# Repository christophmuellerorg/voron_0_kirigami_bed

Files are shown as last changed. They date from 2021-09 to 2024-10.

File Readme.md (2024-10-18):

# What is this?

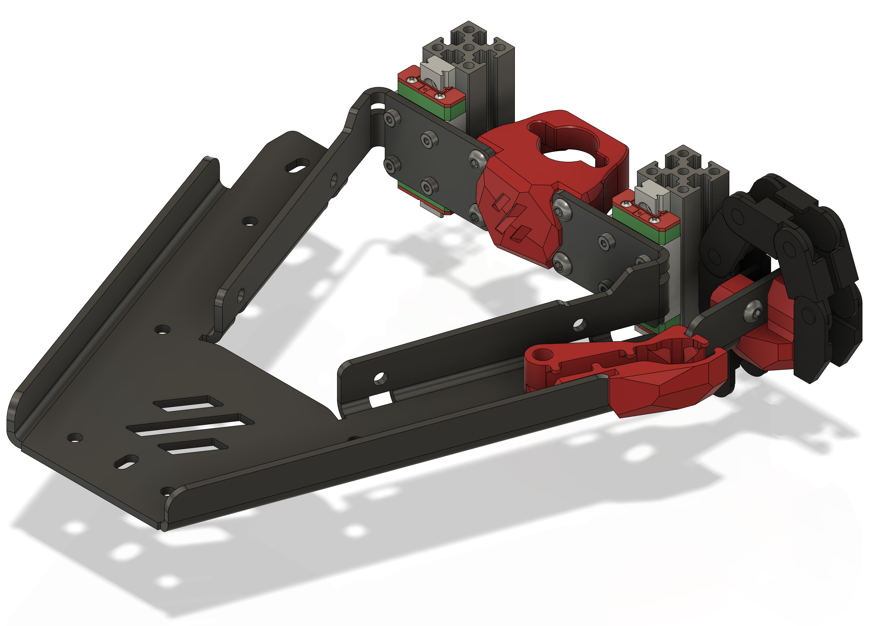
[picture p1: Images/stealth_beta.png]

A laser cut and bent single piece bed concept, trying to implement a lightweight and stiff bed with full access to the mounting screws.

# Where can I get it? 

I only did a small prototype run and will not be able to sell it myself, however there are a few Voron related shops that started stocking it:

- [Deepfriedhero](https://dfh.fm/products/kirigami-beds?variant=43382871556318) (US) 
- [Fabreeko](https://www.fabreeko.com/products/voron-v0-1-kirigami-bed-kit-by-ldo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) (US)
- [3dmakerparts](https://3dmakerparts.com/products/voron-0-1-kirigami-bed) (US)
- [Printyplease](https://www.printyplease.uk/LDOKiri) (UK)
- [Lecktor](https://lecktor.com/en/v0-buildplate/905-kirigami-bed.html) (EU)
- [Unique Prints](https://uniqueprints.shop/shop/buildplate/kirigami-bed-upgrade-for-voron-v0-1/) (AU)
- [Zen3D](https://shop.zen3d.eu/ldo-kirigami-bed-mount-kit) (EU)

I will add additional suppliers _with a vendor role on the Voron discord_ - please contact me on discord or create a pull request with your discord ID.

# Which plastic parts do I need to print?
 
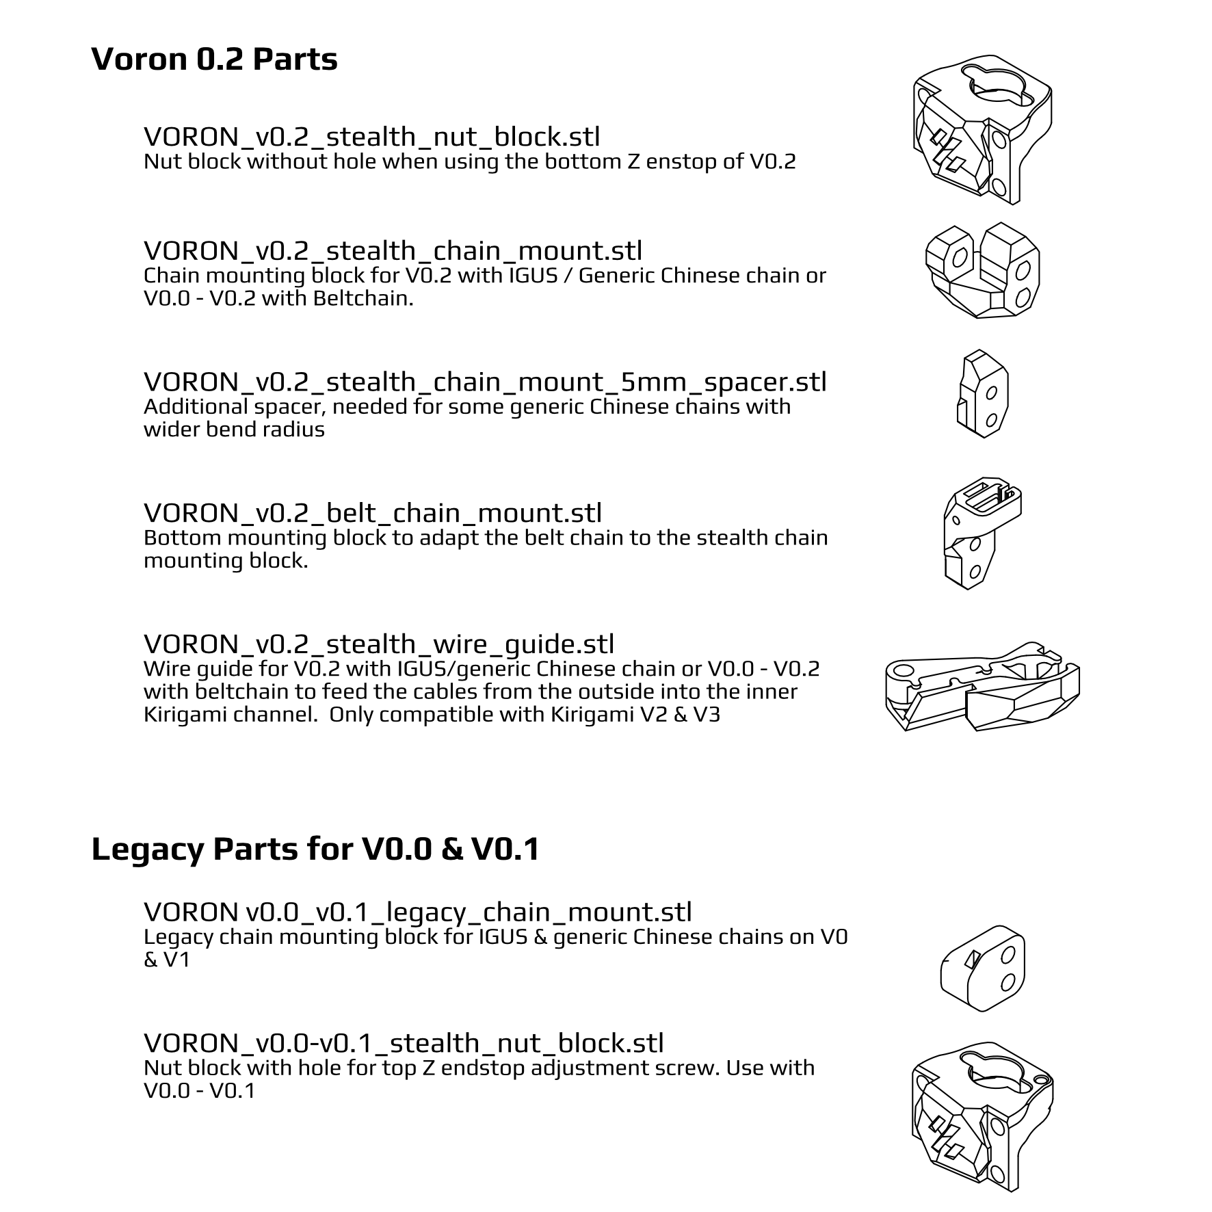
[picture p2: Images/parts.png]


# License

The sheet metal part is available under [CC-BY-SA 4.0](https://creativecommons.org/licenses/by-sa/4.0/) AND [GPL V3.0](https://www.gnu.org/licenses/gpl-3.0.de.html). The plastic parts are partially derived from the existing Voron parts and hence follow the same License, [GPL V3.0](https://www.gnu.org/licenses/gpl-3.0.de.html). 

This means you are allowed to modify and share the sheet metal part under either license, as long as you credit me with a link to this Github repository. You are allowed to produce and sell the part without royalties, a donation on [vorondesign.com](https://vorondesign.com) to fund future development of the Voron project is however appreciated.

# Kiriwhat?

<https://en.wikipedia.org/wiki/Kirigami>

# BOM
- 1x Kirigami Bed
- 8x M2x4 to mount the bed to the carriages
- 4x M3 Heatsets + 4x M3x6 screws for the leadscrew mount
- 4x M3 Heatsets + 2 M3x6 screws for the chain mount
- 1x M3 Heatset + 1 M3x6 screw for the wire guide

# Versions
- V2: added a cutout for the thermal fuse
- V3: slots instead of holes for the bed springs, allowing to adjust the Y offset over a 3mm range to support V0.0 as well as the sherpa mini mod. 

# Installation
The guys from Maple Leaf Makers made a nice tutorial on how to convert the stock bed to Kirigami.

Video tutorial to convert the stock bed to Kirigami (https://www.youtube.com/watch?v=eOnNvhircn8)

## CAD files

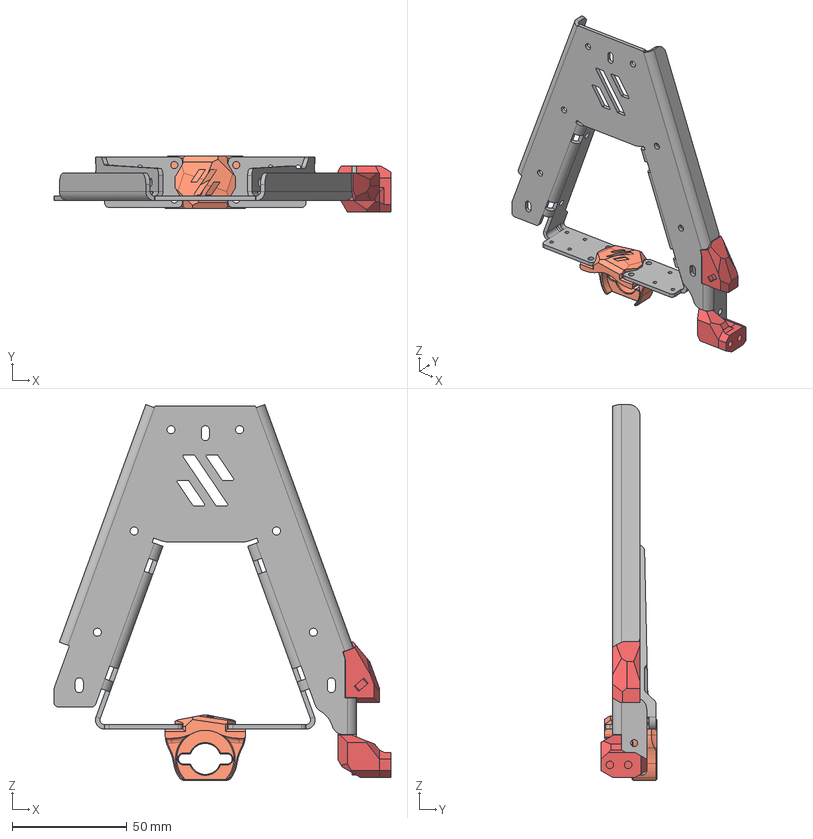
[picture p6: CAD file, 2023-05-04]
CAD/Kirigami_V0.2_stealth_chain_release.step
147.0 x 24.5 x 164.1 mm
VORON_v0.2_stealth_nut_block v3
VORON_v0.2_stealth_chain_mount v2
V0_sheet_metal_bed_v2 v66
VORON_v0.2_stealth_wire_guide.stl v2
VORON_v0.2_stealth_chain_mount_5mm_spacer v2

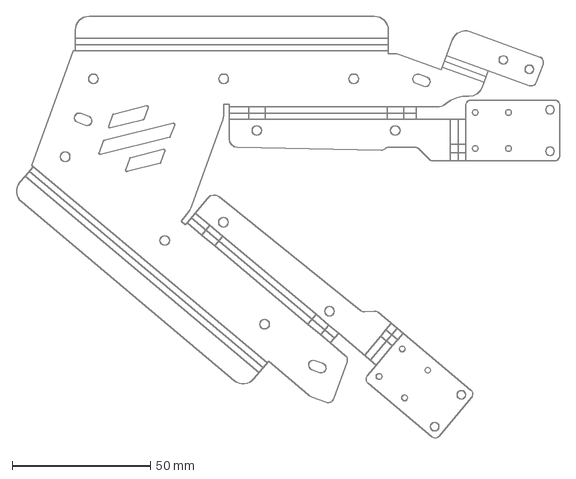
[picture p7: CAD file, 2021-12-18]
CAD/V0_sheet_metal_bed_v3.dxf
196.2 x 152.6 mm

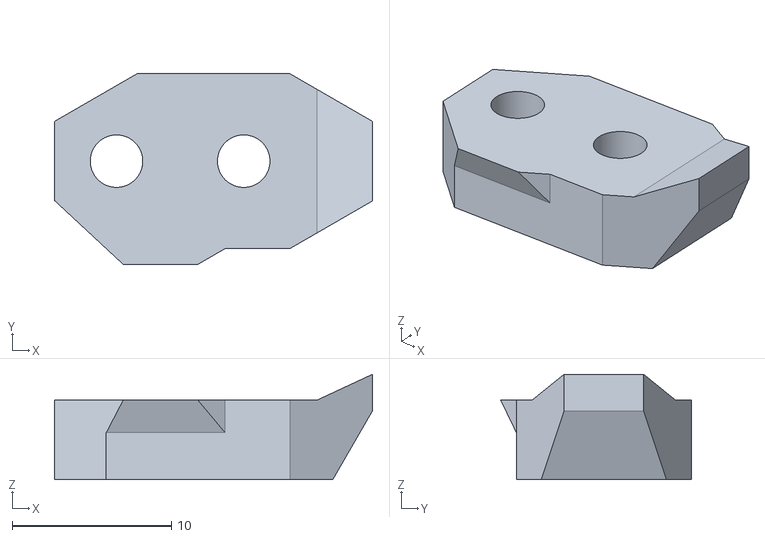
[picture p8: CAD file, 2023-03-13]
STL/VORON_v0.2_stealth_chain_mount_5mm_spacer.stl
20.0 x 12.0 x 6.63

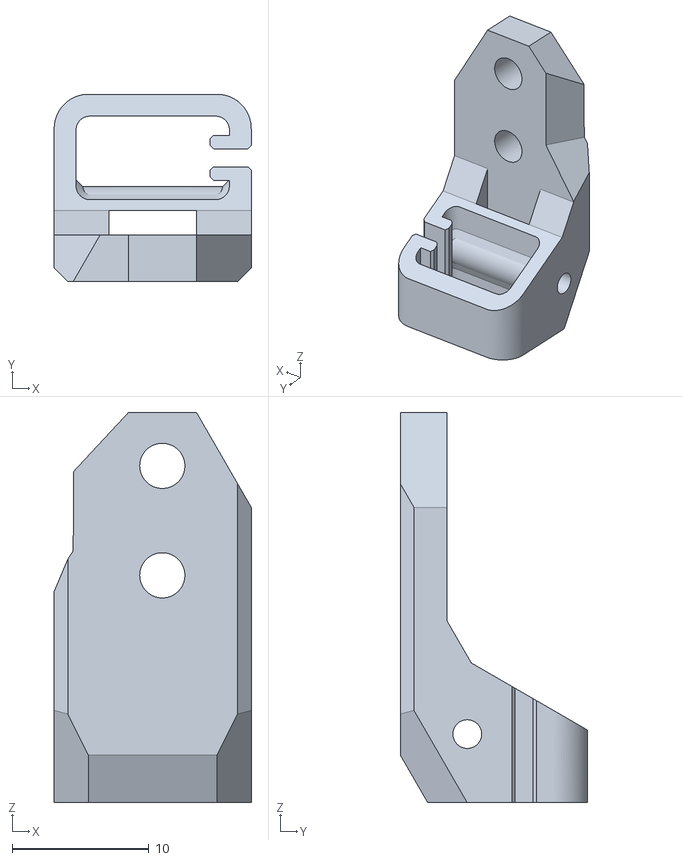
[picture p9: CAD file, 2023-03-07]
STL/VORON_v0.2_belt_chain_mount.stl
14.4 x 13.7 x 28.5

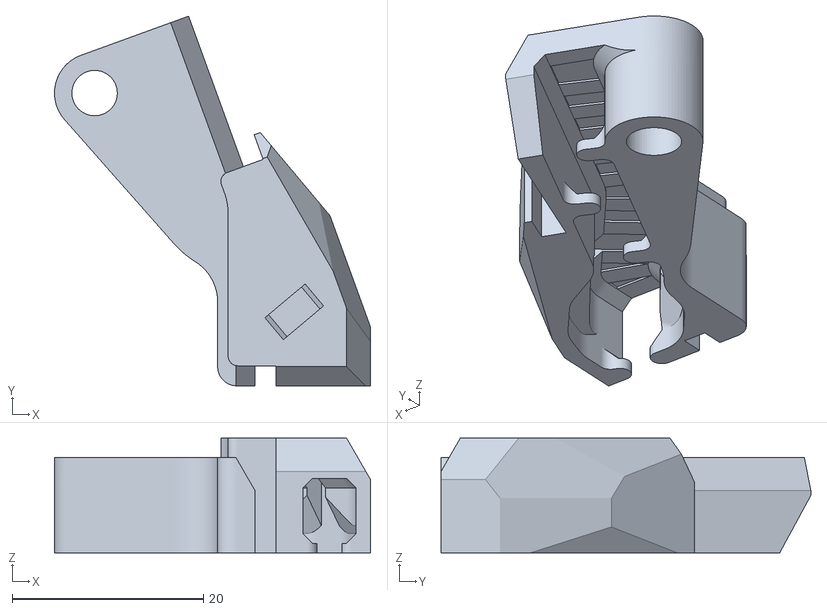
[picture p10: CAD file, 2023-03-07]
STL/VORON_v0.2_stealth_wire_guide.stl
33.1 x 38.7 x 12.0

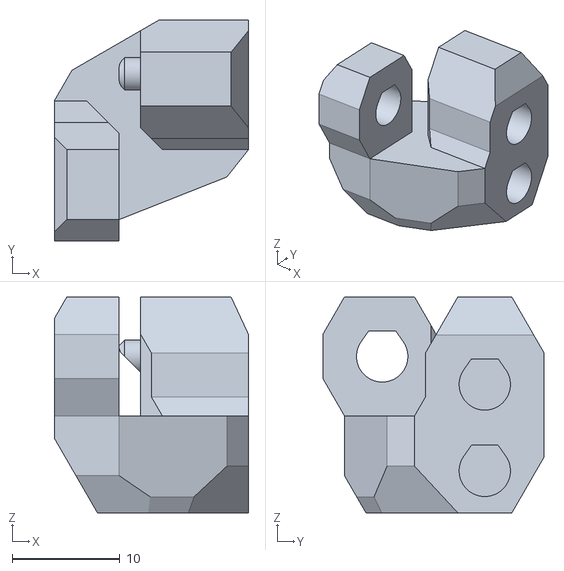
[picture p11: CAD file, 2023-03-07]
STL/VORON_v0.2_stealth_chain_mount.stl
18.0 x 20.5 x 20.0

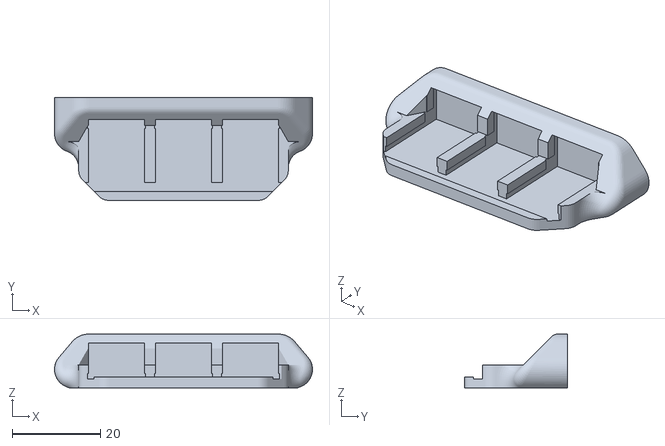
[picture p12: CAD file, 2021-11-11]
STL/kirigami_wago_mount.stl
58.4 x 23.2 x 12.2

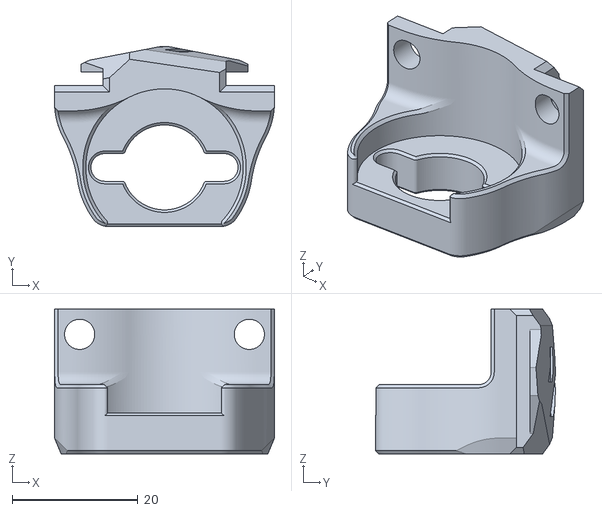
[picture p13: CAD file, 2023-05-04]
STL/VORON_v0.2_stealth_nut_block.stl
35.0 x 28.6 x 23.0

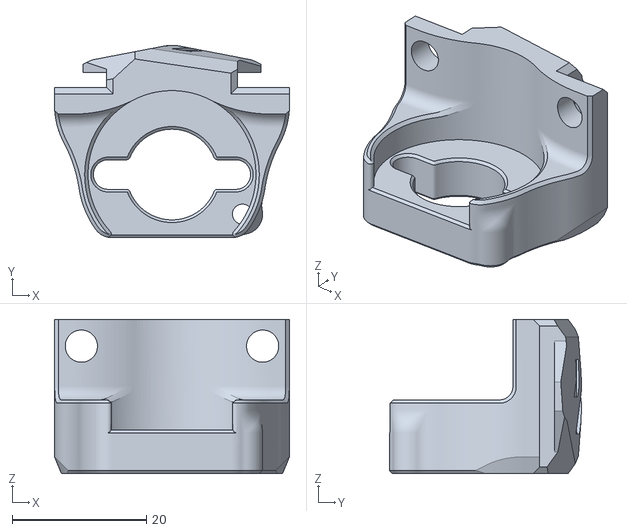
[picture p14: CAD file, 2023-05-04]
STL/VORON_v0.0-v0.1_stealth_nut_block.stl
35.0 x 28.6 x 23.0

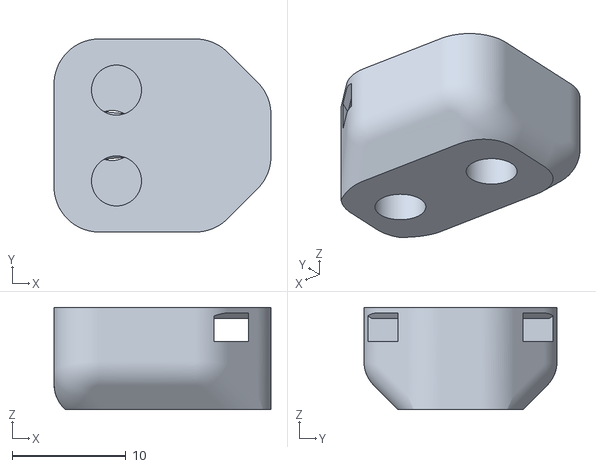
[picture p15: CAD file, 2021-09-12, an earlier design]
STL/VORON v0.0_v0.1_legacy_chain_mount.stl
19.1 x 17.0 x 9.00

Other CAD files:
CAD/Kirigami_V0.2_stealth_chain_release.f3d
CAD/V0_sheet_metal_bed_v3.f3d
CAD/kirigami_wago_mount.f3d

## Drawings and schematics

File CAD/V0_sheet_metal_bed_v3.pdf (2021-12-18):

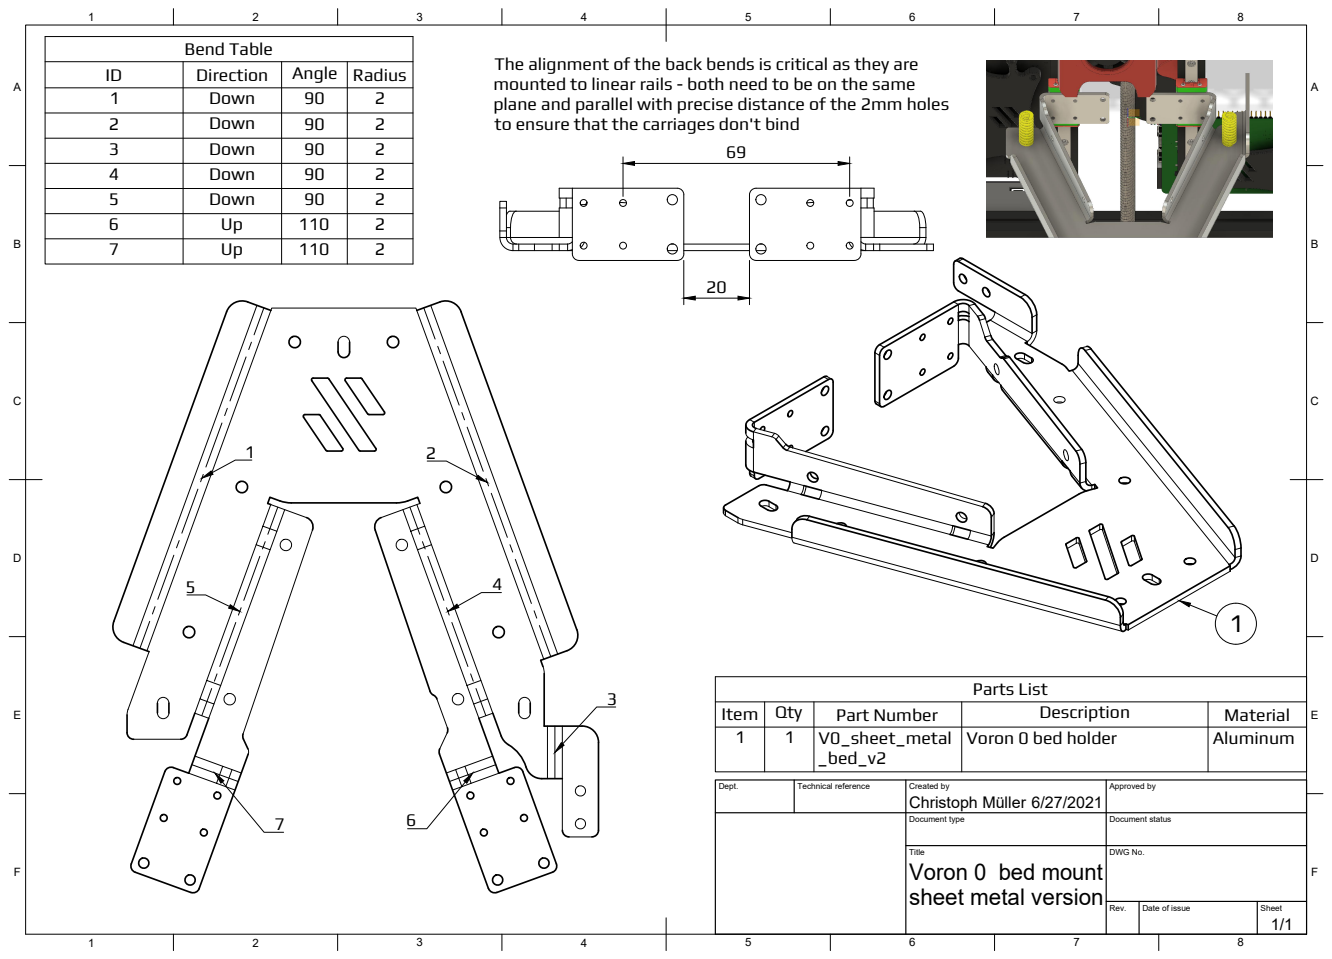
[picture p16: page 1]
Title; DWG No.; Rev.; Date of issue; Sheet; Bend Table; Parts List

The alignment of the back bends is critical as they are
mounted to linear rails - both need to be on the same
plane and parallel with precise distance of the 2mm holes
to ensure that the carriages don't bind

ID | Direction | Angle | Radius
1 | Down | 90 | 2
2 | Down | 90 | 2
3 | Down | 90 | 2
4 | Down | 90 | 2
5 | Down | 90 | 2
6 | Up | 110 | 2
7 | Up | 110 | 2

Item | Qty | Part Number | Description | Material
1 | 1 | V0_sheet_metal _bed_v2 | Voron 0 bed holder | Aluminum

Dept. | Technical reference | Created by Christoph Müller 6/27/2021 | Approved by

Document type | Document status

Voron 0 bed mount
sheet metal version

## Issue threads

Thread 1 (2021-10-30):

the belt z axis mod

dukeGreen, 2021-10-30:
Do you play to support the belt z axis mod?

christophmuellerorg, 2021-11-15:
I won't support it myself, but there is one available here: https://github.com/VoronDesign/VoronUsers/tree/master/printer_mods/MathematicalPotato/v0.1_belted_z_drive/STL/Kirigami_Bed_Mount

Obviously I have not tested it.

Closed 2021-11-20.

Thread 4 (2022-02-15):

Incorrectly sized heat set insert holes on igus_chain_mount.stl

austinvojta, 2022-02-15:
Chain mount piece has 4.4mm diameter holes for heat set inserts. Voron standard for the BOM inserts is 4.7mm (regardless of orientation).

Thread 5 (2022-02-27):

Rail Mounting Screw Spacer

marc-gist, 2022-02-27:
Not an issue, love the mod! Thank you!
That said.  I did print a ~2mm spacer so that I could use the M2x6 screws I already had from the kit for mounting rails.
I think making something like this part of your repository can help those who don't know how to use Fusion to quickly make something like I did from the v0 CAD.

Again, thank you!

Closed 2023-01-04.

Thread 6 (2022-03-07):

stability issues (mounting problem, material?)

dmnkhhn, 2022-03-07:
Hello there,

it's maybe not a general issue but I have stability issues with my Kirigami bed made from 2mm AW5754 (aluminum).

When mounted I can easily push down the front of the bed just by applying little force on the front edge.
This also happens when I adjust the front screw making first layer a hit and miss.

Based on your experience, what might cause this?
Incorrect mounting (screws too loose), incorrect material, rails too sloppy?

I had to use some rather cheapish M2x4mm screws with tiny heads and I have ordered some better ones now. Still I would like to rule out other possibilities.

Any help is appreciated :-)

dmnkhhn, 2022-03-17:
This is still an issue after changing to new rails with a higher preload and new screws that are fully tightened now. I can see it moving when I touch it slightly with one finger. Might be a material issue?

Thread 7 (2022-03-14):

Issues with bed installation

ModMike, 2022-03-14:
Before I describe my issue, let me state, for the record, that I understand this issue has NOTHING to do with you, I am just looking for advice on how to install the bed properly.

I am having a serious issue with binding. Once the bed is tightened the rails rails bind because they are forced out of plane by the bed mounts. I tried tweaking the mounting ears to be in plane, then I designed and printed a part to clamp and the ears, but it only helped a little. Even you tubers such as Vecto 3D had the same issue during his stream, you can see it in his [video](https://www.youtube.com/watch?v=X-Wu85DuZxQ&t=9142s) at the 30 minute mark. He ended up using some TPU spacers but still had binding.

The problem is that factory tolerances and material flexibility make it so that mounting ears are out of plane. The first one I got was beyond tweaking. The replacement I received was better but still binds.

How do you recommend I fix this issue? For now, I ordered 2mm O-Rings to  put between the bed and the rails. I am hoping I can I can toque the screws in different amounts to align the carriers their rails. I just hope to be able to tighten them enough to remove any movement caused by flex between the two.

Let me know your thoughts, my V0.1 has been sitting around for 3 months.

Thanks!

christophmuellerorg, 2023-01-04:
This is not typical, but I have seen some really bad tolerances on steel beds on Aliexpress (looking at you, Funssor...) which would easily cause serious issues due to the bends being out of spec. Check whether the flaps are in one plane and parallel to each other and verify whether the distance between both ends is 20mm - if not contact your vendor, it's a quality control issue on their side.

Closed 2023-01-04.

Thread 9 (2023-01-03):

JST connectors missing from the BOM

KreativeLabs, 2023-01-03:
I purchased this kit but 2pcs JST connectors are missing feom the list to be able to split the thermistor wires. I didn’t have those at hand so I have to pause the conversion. Do I misunderstand something about the build?

christophmuellerorg, 2023-01-04:
The PCB is not part of the Kirigami bed project but an addition by LDO I have no control over.

KreativeLabs, 2023-01-04:
Oh I see :)

Closed 2023-01-04.

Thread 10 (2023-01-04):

STL' corrupted?

bsjoelund, 2023-01-04:
Downloaded the stl's and no file can be opened in any slicer.

christophmuellerorg, 2023-01-04:
Nothing has changed and the files are fine, just tried - likely user error, try the download zip option of the "code" button on the repository main page.

Closed 2023-01-04.

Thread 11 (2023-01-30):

Material type not mentioned in README

west1012, 2023-01-30:
Hi.  Would it be possible to get the material type chosen (I am guessing 5052 aluminum) in the README.md for the project?  I see in the PDF file in the CAD file the part is to be made out of "aluminum", but it took me a while to see it there.  I'm guessing I'm not the only one who hasn't been able to find it before.

Thanks!

VersedHG, 2023-05-29:
LDO use 6061 alu.

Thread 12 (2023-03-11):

Chain mount problem - chain radius too small

hmouridsen, 2023-03-11:
Hi

I think the [VORON_v0.2_stealth_chain_mount.stl] should be a little bigger. I don't know if chains are different, but I've bought the one listed in the 0.2 bom. I feel the bending radius is too small for the chain, witch means my printer struggles with the z-axis due to chain resistance
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

christophmuellerorg, 2023-03-11:
Hi, can you measure the distance between the profile and the inside of your chain for the worst possible configuration, i.e. the top chain segment being parallel to the ground?

Technically this mount is already widened relative to the original design and based on the chains I have here it should just fit. I might add a dragchain spacer to add a few additional mm if required.

Best,
Christoph

hmouridsen, 2023-03-12:
Hi Christoph

First of all thanks for sharing your work.

I'm not sure if I understand you clearly, but I for my chain to move freely, without resistance, I need 2mm more. Witch means the chain mount should be 12mm instead of 10mm. A spacer could be an easy solution as well.

My chain starts to move freely at 27mm bend radius (with the top link parallel to the ground), and at the moment I measure about 24mm

At first I mounted the 0.1 chain mount witch is 9mm wide, and it made my z motor buzz.

hmouridsen, 2023-03-12:
Hi

I did some spacer testing, and 15mm seems to be the correct size for my chain, but I guess it can vary a lot from chain to chain

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

christophmuellerorg, 2023-03-13:
I just added a 5mm spacer, please give it a try and let me know whether it works.

hmouridsen, 2023-03-15:
> I just added a 5mm spacer, please give it a try and let me know whether it works.

Thanks a million - it's perfect - chain is absolutely moving freely now

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

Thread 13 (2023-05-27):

v0.2 belt chain mount question

chrisheninger, 2023-05-27:
Hi Christoph (or anyone reading these issues that might know the answer!)–

I'm building a v0.2 kit from Formbot3d.

It came with a kirigami bed– and I'm trying to figure out where the `VORON_v0.2_belt_chain_mount` belongs. I've noticed a lot of the pictures/diagrams in the repo show different variations/versions and I haven't seemed to be able to find anything online showing different angles of the v0.2.

Here's a photo:

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

Thank you!

Edit: After thinking about it a little longer... I'm realizing that I don't need the "belt chain mount" because I'm using the "stealth chain mount" and spacer?

YungChin95, 2023-05-29:
Yes, the belt chain mount is if you're using the Belt Chain usermod. So it's not needed for you

Closed 2023-05-29.

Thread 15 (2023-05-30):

Tools stl directory

ningpj, 2023-05-30:
Your earlier release included a tools subdir with k-bed bender and dual rail alignment jig.
Did you mean to drop it when you published the updated version? No problem if you did, just checking.

Closed 2024-11-06.

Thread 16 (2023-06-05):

Formbot bed is too thick for the Stealth Nut Block

Janus303, 2023-06-05:
We are building the V0.2 kit from FormBot, which comes with a kirigami bed. The Stealth Nut Block part will not fit, even before installing heat set inserts. It may be due to the thickness of the powder coat. I would like to edit that part to make it a little roomier, but I am not seeing the CAD file.

Kagee, 2023-06-05:
The nut block is part of [Kirigami_V0.2_stealth_chain_release.f3d](https://github.com/christophmuellerorg/voron_0_kirigami_bed/blob/master/CAD/Kirigami_V0.2_stealth_chain_release.f3d).

The CAD calls for 2.0 mm and a 20 mm gap. What are the measurements on the FormBot kit? LDO kit is a hair's breath *below* spec.

Janus303, 2023-06-06:
The thickness when measured from top to bottom is 2.5mm. The thickness when measured in the middle is 2.3mm. So there is a bit of a bow, but even if it were flat it would be too thick. If it were flat and had no powder coat, it'd probably be right on the money.

christophmuellerorg, 2023-06-06:
Ultimately this is an issue of Formbot not producing spec parts and I can only design for parts I have at hand - Formbot never sent me their bed for feedback like LDO did. I am somewhat hesitant to make more variants as the current part count is already confusing people.

Janus303, 2023-06-07:
I edited the slot to make it a bit wider which is fine for my purposes. It seems like a long term solution would be to redesign the nut block to be more tolerant of variance in thickness as opposed to making more variants of the part.

SrgntBallistic, 2023-06-24:
> Ultimately this is an issue of Formbot not producing spec parts and I can only design for parts I have at hand - Formbot never sent me their bed for feedback like LDO did. I am somewhat hesitant to make more variants as the current part count is already confusing people.

@christophmuellerorg
I'm planning to buy a couple parts from their web store. Obviously it'd be best for them to work directly with you. But many people buy their kits and will end up posting issues here.

Can I send you one of their bed frames? You can possibly make any changes to printed parts or have disclaimers specifically about the bed?

I posted another issue about the thermal fuse. LMK Thanks

Janus303, 2023-06-24:
FWIW, Formbot sent us modified STLs which also did not work. We ended up just buying the LDO bed for $25 and it works perfectly.

bethouxa, 2023-11-08:
Hello, FYI this is stil the case, just got a kit and the bed is 2.2mm (+/- 0.05) thick.
Also, the printed parts they provide seems to be the same as yours and does not fit without significant force.

Jostymon, 2025-02-12:
I got my Formbot kit and everything was fine. Mine is 2.08

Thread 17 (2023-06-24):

Formbot Bed Thermal Fuse Collides with Frame

SrgntBallistic, 2023-06-24:
My Formbot V0.2 kit includes a thermal fuse and has a pre-drilled/tapped hole for mounting it.

I mounted it in this location and with the bed to the rear-most position allowed by the bed screw slots the fuse collides with the bed frame on the slanted transition bit before the fuse cutout.

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

With the collision I'm not able to lower the bed enough to ensure the nozzle doesn't collide with the bed in that corner.

I can move the bed forward in the slots but I'll end up losing about 3mm of volume in the Y which I'm trying to avoid.

I looked at the V0 drawing for the bed and they don't seem to state how far away from the edge the fuse should be mounted. So I don't think the Formbot bed is out of spec in that regard.
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

I'm debating a few solutions

1. Re drilling/tapping the mounting hole for the fuse
2. Removing some material from the fuse
3. Removing some material from the bed
4. Mounting the fuse to the silicone pad with RTV

I'm not suggesting any revisions to account for this. Maybe just a callout noting that there could be issues or a suggestion for handling this.

christophmuellerorg, 2023-06-27:
Please open a complaint with Formbot so that they can fix it in their next batch, should be solvable by placing the fuse mounting hole further inside towards the center of the bed.

I use a Fermio bed here which seems to just work. The cutout was introduced before the slot which allows to shift the bed backwards and forwards for fine tuning of the location, debending on the extruder used. I don't think it would be wise to extend the fuse cutout even further back, considering the stability of the bed.

SrgntBallistic, 2023-06-27:
> Please open a complaint with Formbot so that they can fix it in their next batch, should be solvable by placing the fuse mounting hole further inside towards the center of the bed.
>
> I use a Fermio bed here which seems to just work. The cutout was introduced before the slot which allows to shift the bed backwards and forwards for fine tuning of the location, debending on the extruder used. I don't think it would be wise to extend the fuse cutout even further back, considering the stability of the bed.

Thanks Christoph. Feel free to close this. I just wanted to bring it to your attention. I have a list of issues/concerns/improvements I'm giving to Formbot. They provided this kit for review.

In another post about the Formbot frame thickness I noted I can send you one of their frames. Please let me know if you'd like one. I ordered a number of items from their site including an extra frame. I'm happy to send it along.

Thanks for the great mod!

Closed 2023-08-21.

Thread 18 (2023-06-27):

chain too close to back panel

Matszwe02, 2023-06-27:
The cable chain is too close to the back panel and it keeps scratching the acrylic, in my case. I think there's a tiny bit of play to this chain, but it's hardly achieveable to have it not scratch.
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

christophmuellerorg, 2023-06-27:
Seems like you mounted the end cap of the chain the wrong way around, compare to
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

Finally, there are dozens of chains out there and I cannot test all - for example, I have never seen this one in particular. The location of the chain mount is identical to the stock design, so if your chain does not work well you would have the same trouble. The V0 is a tight design and there is very little clearance in this location, scratches can happen and are purely cosmetic.

Matszwe02, 2023-06-28:
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

Hi. Thanks for the reply. I have some chain that came with a formbot kit, which bends "the wrong way", so I had to rotate it. Now I figured out that my electronics may have a tight fit and cause the acrylic to bend towards the chain

Closed 2023-06-27.

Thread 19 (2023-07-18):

Bed screw slots

bartlammers, 2023-07-18:
Is it an idea to explain what position of the slots needs to be used for what printer?
If I recall correctly it is the front for V0.1 and the rear for V0 and V0.2?

Perhaps also add a spacer like https://github.com/stvptrsn/Printer_Stuff/blob/main/Voron_0/Kirigami/Kirigami_Bed_Spacer.stl to align it correctly.

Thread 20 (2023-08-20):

Thicker body for heat set inserts in V0.2 nut block?

Kagee, 2023-08-20:
Is there a reason the bottom of the nut block can not be slightly thicker, thus think enough to have a bottom for the heat set inserts, and making it fail and press them through?

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

Kagee, 2023-08-24:
Hmm, yes, but would not V0.0 users use the other STL with a screw hole for the top-mounted Z-endstop anyway? So in theory the v0.2 block could be thicker?

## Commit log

2021-11-10 mounting of the plastic parts
2021-11-11 added wago mounts
    [WAGO_221-412_3x2-mount-kirigami.f3d, kirigami_wago_mount.stl]
2021-11-23 + printyplease
2021-12-07 alignment tool added
    [v0_z_rail_dual_align.stl]
2021-12-18 Version 3: Slots for adjustable Y offset
    [V0_sheet_metal_bed_v2.dxf, V0_sheet_metal_bed_v2.f3d, V0_sheet_metal_bed_v2.step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]
2022-01-09 Added step with plastic parts
    [V0_sheet_metal_bed_with_plastic_parts_v3.step]
2023-03-07 v0.2 beta parts
    [K-Bed_Bender-v2.stl, VORON v0.0_v0.1_legacy_chain_mount.stl, VORON_v0.2_belt_chain_mount.stl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]
2023-03-13 5mm spacer added
    [VORON_v0.2_stealth_chain_mount_5mm_spacer.stl]
2023-05-04 old mounting guide removed
2023-05-11 readding the wago mount deleted by mistake, sorry
    [kirigami_wago_mount.f3d, kirigami_wago_mount.stl]
2024-10-18 Update Readme.md
    😢
